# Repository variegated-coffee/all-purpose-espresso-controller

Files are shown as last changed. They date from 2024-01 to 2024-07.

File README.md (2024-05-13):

# All Purpose Espresso Controller

Espresso electronics are usually proprietary affairs with little to no expandability. The purpose of this project is to give everyone an open source alternative with lots of features and flexibility. 

It is designed to be useful in many different espresso machines, and for many different hardware configurations. It has the same PCB size as many very common Gicar controllers, making it fairly easy to swap this board into your existing enclosure. It also comes with screw holes, so a 3D printed enclosure is another option.

There's also a [corresponding 100-240 VAC board](https://github.com/open-lcc/all-purpose-espresso-controller-hv-board), with relays and an AC/DC converter, designed to also fit into those same Gicar enclosures.

## High-level features

* RP2040 microcontroller with 2 MB of program flash, and 2 MB of settings flash
* ESP32-S3 for extra processing power and Wi-fi/Bluetooth connectivity
* SD card reader
* Plenty of IO, at 12V, 5V and 3V3 levels
* Dedicated connector for a UART based user interface device, like an [Open LCC](https://github.com/open-lcc/open-lcc-board) or a Nextion touchscreen (selectable 5V or 3V3 level)
* EyeSPI connector for ESP32-S3
* ADS124S08 ADC (intended for e.g. pressure transducers or NTCs)
* FDC1004 Capacitance-to-digital (inteded for e.g. water level probes or capitance based controls)
* QWIIC ports (one per microcontroller) for additional expandability

[IBOM](https://raw.githack.com/open-lcc/all-purpose-espresso-controller/r0d/manufacturing-data/r0d/ibom.html)

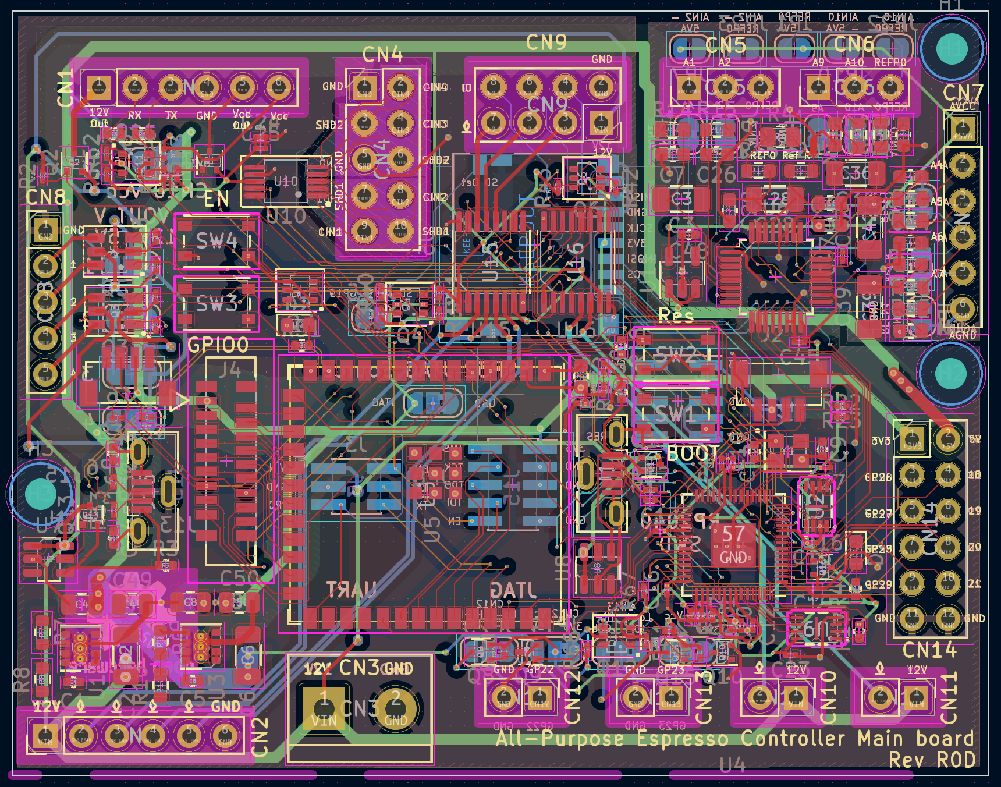
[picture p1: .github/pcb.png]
PCB

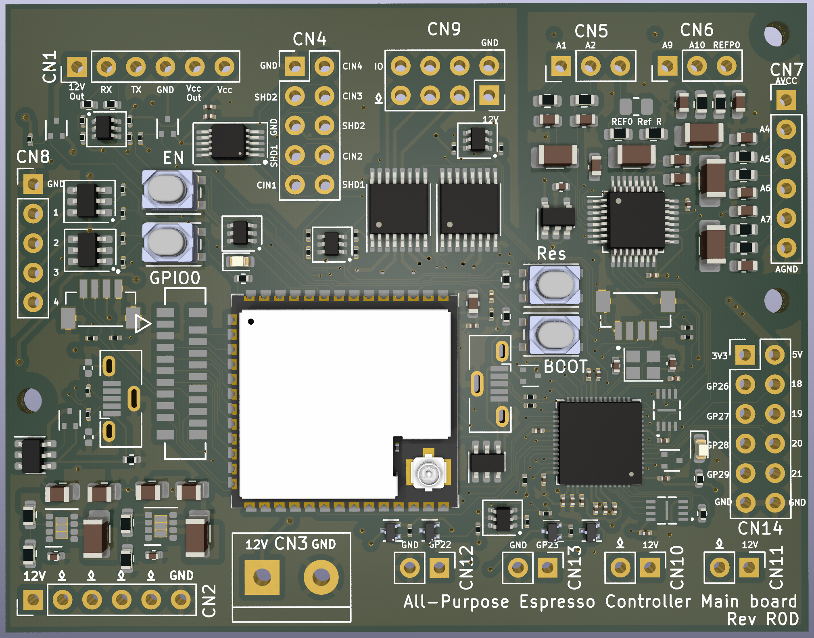
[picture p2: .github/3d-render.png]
3D render PCB 3D render

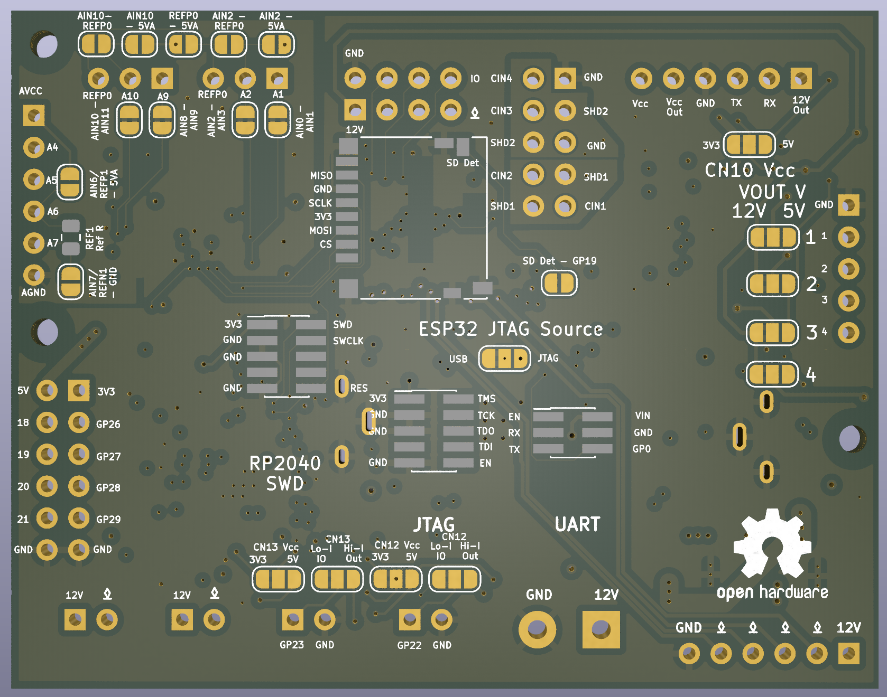
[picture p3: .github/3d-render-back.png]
3D render back PCB 3D render of back side


## Project status

The current hardware revision is R0D. It hasn't been manufactured yet, and you shouldn't be the first one to do it.

## Disclaimer

Anything you do with this, you do at your own risk. This hardware hasn't even been manufactured by it's creator yet. Your machine uses both line voltage power, high pressured hot water, steam and other dangerous components. You *really* shouldn't be using this yet; in fact, you shouldn't even consider it. Risks include but are not limited to, damaging your machine, personal injury, property damage and summoning dead Cthulhu from his sleep at R'lyeh.

## Connectivity
* CN1 - Display Connector, either for Open LCC or a Nextion Display
  * UART (selectable 3V3 or 5V, default 3V3)
    * JP9 selects voltage
    * RP2040 UART0
    * ESP32 GPIO17/GPIO14
  * 1x 12V output (SR2 DRAIN6)
  * 1x 3V3 output (SR2 DRAIN7)
  * 1 3V3/5V pin and GND pin
* CN2 - HV Board Connector
  * 12V and GND
  * 4 Open drains (SR1 DRAIN0-3)
* CN3 - Separate PSU Connector
  * 12V and GND
* CN4 - Capacitive sense connector
* CN5 - ADC port
  * See note below
* CN6 - ADC port
  * See note below
* CN7 - ADC port
  * See note below
* CN8 - Outputs
  * 4x 5V/12V Outputs
    * Voltage selectable by JP4-6/JP16
  * GND
* CN9 - Open drains and 3V3 IO
  * 3x Open drains (SR1 DRAIN5-7)
  * 3x 3V3 IO (RP2040 GPIO12-14)
  * 12V/GND
* CN10 - Open drain
  * SR2 DRAIN1
  * 12V
* CN11 - Open drain
  * SR2 DRAIN0
  * 12V
* CN12 - 3V3/5V GPIO
  * RP2040 GPIO22
  * Shifted through MOSFET level shifter
  * Can be switched to a 500 mA output with solder jumper
  * GND
* CN13 - 3V3/5V GPIO
  * RP2040 GPIO23
  * Shifted through MOSFET level shifter
  * Can be switched to a 500 mA output with solder jumper
  * GND
* CN14 - GPIO
  * RP2040 GPIO18-21
    * GP19 can be connected to SD Card Detect via a solder jumper
    * GP21 is also connected to an LED
  * RP2040 GPIO26-29
    * ADC Capable

### ADC
By default, CN5 and CN6 are configured for a ratiometric measurement. In order to use it as such, you need to fit a reference resistor for REF0. The reference resistor needs to be larger than the measured values (e.g. for a PT100, use a 400 ohm resistor), and needs to be high accuracy and low drift. 

AIN1-2, AIN4-7, and AIN9-10 are all outfitted with RC filters, as is REF0. The board is also designed in such a way that you can, by sacrificing an RC filter, convert a channel to instead use an upstream resistor divider. 

The ADS124S08 features two external references (REF0 and REF1), as well as an internal 2.5V reference. AIN6-7 double as REFP1/REFN1. The board is designed with footprints for a reference resistor.

#### Common configurations

##### PT100 RTD

##### PT1000 RTD

##### 50k NTC - Ratiometric

##### 50k NTC - Resistor divider

##### 0.3 – 4.5 V Pressure trandducer - 5 V Reference

##### 0.3 – 4.5 V Pressure trandducer - Resistor divider

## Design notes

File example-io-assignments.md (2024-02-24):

## Lelit Bianca v2 with Open LCC, Gear Pump, and Pump Pressure Transducer

### IO Assignment

* CN10 - Open LCC
* CN1 - Water level probe
* CN2 - Water tank level switch
* CN3 - Service Boiler NTC
* CN4 - Brew Boiler NTC
* CN5 - Brew Boiler SSR
* CN9 - Service Boiler SSR
* CN7 - Brew Switch
* JP2 Pin 3 - Water line / Low flow solenoid
* JP2 Pin 4 - Service boiler solenoid
* CN6 Pin 3 - Gear pump speed PWM
* CN6 Pin 5 - Gear Pump Tacheometer Input
* J11 Pin 2 - Pressure Transducer Analog Input

### Configuration

* ADC Vcc - 5V
* CN10 Vcc - 3V3
* DNF ESP32

## Rancilio Silvia with ESP32, SSD1309 display, Rotary encoder, Gear Pump, and Pump Pressure Transducer

### IO Assignment

* CN10 - Open LCC
* CN4 - Boiler NTC
* CN5 - Boiler SSR
* J12 Pin 8 - Display MOSI
* J12 Pin 4 - Display SCLK
* J12 Pin 6 - Display RES
* J12 Pin 10 - Display DC
* Hard-wire Display CS
* CN7 - Brew Switch
* CN2 - Water Switch
* J12 Pin 9 - Steam Switch
* J12 Pin 3 - Rotary Encoder Clk
* J12 Pin 5 - Rotary Encoder D
* J12 Pin 7 - Rotary Encoder SW
* JP2 Pin 4 - Three-way solenoid
* CN6 Pin 3 - Gear pump speed PWM
* CN6 Pin 5 - Gear Pump Tacheometer Input
* J11 Pin 2 - Pressure Transducer Analog Input

### Configuration

* ADC Vcc - 5V
* CN10 Vcc - 3V3
* DNF ESP32

## Worst case scenario IO Assignment

### Machine spec

* 2 group triple boiler (2 coffee, 1 service), all PID controlled with level sensors
* Dual PWM gear pumps for coffee boilers
* Single rotary pumps for service boiler
* Dual flow sensors
* Triple NTC thermistors
* Triple pressure transducers
* Five solenoids (3 line solenoids, 2 three-way group solenoid)
* Two brew microswitches
* One water tank level switch

### IO Assignments

* Brew Boiler 1 HE Relay - JP2 Pin 2
* Brew Boiler 2 HE Relay - JP2 Pin 3
* Service Boiler HE Relay - JP2 Pin 4
* Service Boiler Rotary Pump Relay - JP2 Pin 5
* Gear pump 1 PWM - CN6 Pin 3
* Gear pump 2 PWM - CN6 Pin 5
* Flow sensor 1 - J12 Pin 4 GP18
* Flow sensor 2 - J12 Pin 6 GP19
* NTC Brew 1 - CN3
* NTC Brew 2 - CN4
* NTC Service - J11 Pin 2
* Pressure Transducer 1 - J12 Pin 3 GP26
* Pressure Transducer 2 - J12 Pin 5 GP27
* Pressure Transducer 3 - J12 Pin 7 GP28
* Brew Boiler 1 Level sensor - J14 Pin 2
* Brew Boiler 2 Level sensor - J14 Pin 4
* Service Boiler Level sensor - CN1
* Water Tank Switch - CN6 Pin 7
* Brew switch 1 - CN2
* Brew switch 2 - CN7
* Solenoid 1 - J10 Pin 2
* Solenoid 2 - J10 Pin 3
* Solenoid 3 - CN6 Pin 4
* Solenoid 4 - CN6 Pin 6
* Solenoid 5 - CN6 Pin 8
* ESP32 UART J12 Pin 8 GP20
* ESP32 UART J12 Pin 10 GP21
* ESP32 Firmware update J12 Pin 9 GP29

#### Free pins

* CN5 (Output)
* CN9 (Output)
* J10 Pin 4 (Output)
* J11 Pin 3 (ADC)
* J14 Pin 7 (Capacitance)

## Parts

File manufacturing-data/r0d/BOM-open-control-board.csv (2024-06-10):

Comment | Designator | Footprint | LCSC
0R | R32,R33 | R_0201_0603Metric | C106228
18K7 | R13,R3 | R_0402_1005Metric | C11476
1K | R5,R6 | R_0402_1005Metric | C11702
Q_PMOS-E_DUAL_Generic_SEP_S1G1D2S2G2D1 | Q3,Q5 | TSOT-23-6 | C124461
10 μF, 25 V, X7R | C2,C6 | C_1206_3216Metric | C13585
DMP21D0UT-7 | Q1,Q15,Q2,Q8 | SOT-523 | C150733
6.8 nF, 50V | C1,C48,C5 | C_0402_1005Metric | C1542
12 pF | C10,C9 | C_0402_1005Metric | C1547
330 nF | C46 | C_0603_1608Metric | C159798
BM04B-SRSS-TB(LF)(SN) | J17,J2 | JST_BM04B-SRSS-TB(LF)(SN) | C160390
RP2040 | U4 | QFN-56-1EP_7x7mm_P0.4mm_EP3.2x3.2mm | C2040
DMG1012T-7 | Q10,Q13,Q14,Q16,Q9 | SOT-523 | C20512
DMN63D8LDW | Q11,Q12,Q4,Q6,Q7 | SOT-363_SC-70-6 | C211422
STPIC6C595TTR | U15,U16 | TSSOP-16_4.4x5mm_P0.65mm | C222081
KT-0603W | D1,D2 | LED_0603_1608Metric | C2290
75K | R9 | R_0603_1608Metric | C23242
24K | R10 | R_0603_1608Metric | C23352
10K | R1,R19,R2,R22,R23,R28,R29,R30,R34,R36,R37,R38,R39,R40,R41,R42,R43,R59,R61,R62,R63,R64,R65,R67,R68,R69,R70 | R_0201_0603Metric | C242159
120R | R31,R44 | R_0402_1005Metric | C25079
4K7 | R17,R18 | R_0402_1005Metric | C25900
SW_Push | SW1,SW2,SW3,SW4 | SW4_PTS815 SJM 250 SMTR LFS_CNK | C2689510
27R | R11,R12 | R_0201_0603Metric | C273268
47R | R45,R46,R47,R48,R49 | R_0201_0603Metric | C273279
71K5 | R7 | R_0603_1608Metric | C278547
W25Q16JVUXIQ | U2,U9 | W25Q16JVUXIQ_WIN | C2843335
FDC1004 | U10 | VSSOP-10_3x3mm_P0.5mm | C2865994
ADS124S08IPBSR | U6 | LQFP-32_5x5mm_P0.5mm | C2870171
ESP32-S3-WROOM-1 | U5 | ESP32-S3-WROOM-1U | C3013946
Molex_0525591853 | J4 | CON_525591853_MOL | C3169221
5.1 nF, C0G | C26,C29,C35,C37,C38,C40,C41,C43,C44,C7 | C_0603_1608Metric | C3884201
100 nF, >10V, X6S | C12,C13,C14,C15,C16,C17,C18,C19,C20,C21,C23,C24,C27,C31,C45,C53,C54 | C_0201_0603Metric | C412246
1 uF, >6.3V, X5R | C11,C22,C25,C30,C47,C51 | C_0201_0603Metric | C426073
22 uF, 10V, X7T | C4,C49,C50,C8 | C_0805_2012Metric | C45783
LM5050-1 | U7,U8 | TSOT-23-6 | C473393
TPS82130 | U1,U3 | Texas_SIL0008D_MicroSiP-8-1EP_2.8x3mm_P0.65mm_EP1.1x1.9mm_ThermalVias | C473914
6K04 1% | R14,R15,R21,R24,R25,R26,R27,R35 | R_0603_1608Metric | C513554
XYDBPCNANF-12MHZ | Y1 | Crystal_SMD_2520-4Pin_2.5x2.0mm | C521567
USB_B_Micro | J1,J16 | USB_Micro-B_Molex-105133-0001 | C586226
22 uF, 6.3V, X5R | C32 | C_0603_1608Metric | C59461
TC2014-5.0VxCTTR | U11 | SOT-23-5 | C626522
4K99 1% | R16,R20 | R_0603_1608Metric | C705903
51 nF, C0G | C28,C3,C36 | C_1206_3216Metric | C711044
13K3 | R8 | R_0603_1608Metric | C719290

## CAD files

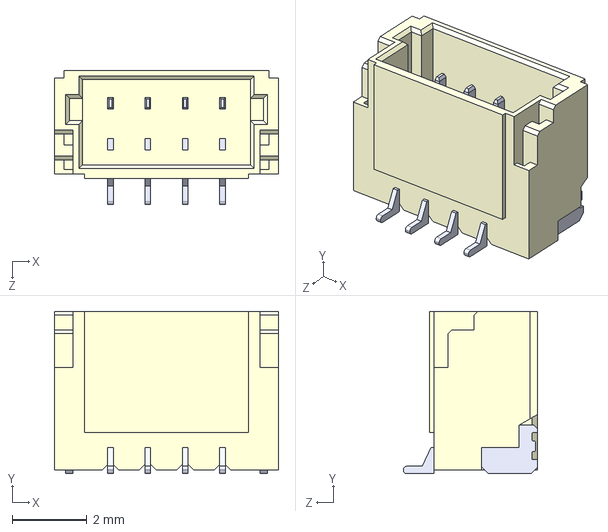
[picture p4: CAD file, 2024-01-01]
BM04B-SRSS-TB_LF__SN_/BM04B-SRSS-TB_LF__SN_.step
6.00 x 4.35 x 3.60 mm

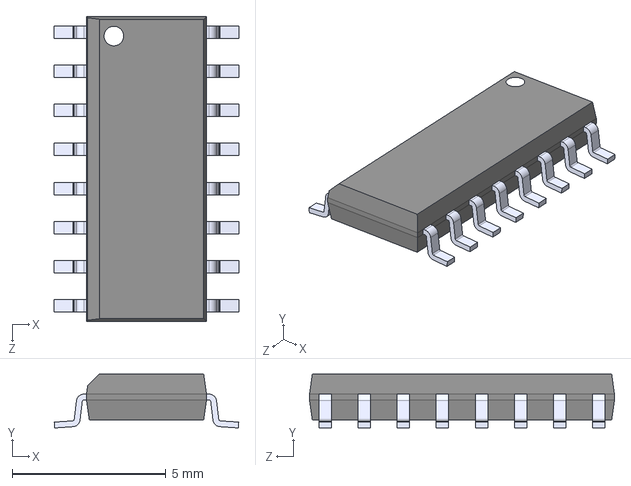
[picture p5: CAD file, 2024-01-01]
TPIC6C595DG4/TPIC6C595DG4.step
5.99 x 1.75 x 9.91 mm

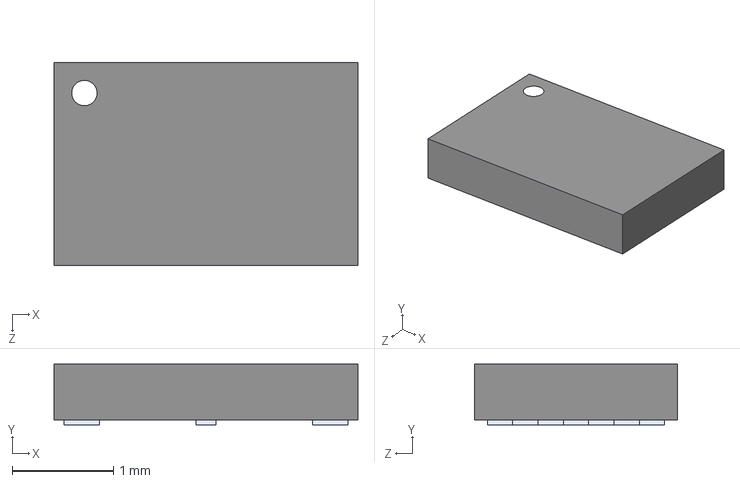
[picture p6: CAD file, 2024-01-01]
W25Q16JVUXIQ/W25Q16JVUXIQ.step
3.00 x 0.6 x 2.00 mm

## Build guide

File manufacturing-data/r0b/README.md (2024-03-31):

# Manufacturing with JLCPCB

Manufacturing of R0B was done with JLCPCB, including PCB Assembly.

The following settings were used:

### PCB Prototype
* Gerber file: GERBER-open-control-board_Y54
* Build Time: 3 days (PCBA Only)
* Base Material: FR-4 
* Layers: 4
* Dimension: 69 mm* 54 mm 
* PCB Qty: 5
* Product Type: Industrial/Consumer electronics 
* Different Design: 1
* Delivery Format: Single PCB 
* PCB Thickness: 1.6
* Impedance Control: no No requirement 
* Layer Sequence: 
* PCB Color: Green 
* Silkscreen: White
* Material Type: FR4-Standard TG 135-140 
* Via Covering: Epoxy Filled & Capped
* Surface Finish: HASL(with lead) 
* Deburring/Edge rounding: No
* Outer Copper Weight: 1 oz 
* Inner Copper Weight: 0.5 oz
* Gold Fingers: No 
* Flying Probe Test: Fully Test
* Castellated Holes: no 
* Edge Plating: No
* Remove Order Number: No 
* Min via hole size/diameter: 0.3mm/(0.4/0.45mm)
* 4-Wire Kelvin Test: No 
* Paper between PCBs: No
* Appearance Quality: IPC Class 2 Standard 
* Confirm Production file: Yes
* Silkscreen Technology: Ink-jet/Screen Printing Silkscreen 
* Package Box: With JLCPCB logo
* Board Outline Tolerance: ±0.2mm(Regular)

The observant will note that this is the default settings, except Via Covering and Confirm Production File.

### PCBA

* PCBA Type: Economic
* Assembly Side: Top Side
* PCBA Qty: 5
* Tooling holes: Added by JLCPCB
* Confirm Parts Placement: Yes
* Photo Confirmation: No
* Board Cleaning: No
* Conformal Coating: No
* Bake Components: No
* Packaging: Antistatic bubble film
* Depanel boards & edge rail before delivery: No
* Solder Paste: Sn96.5%, Ag3.0%, Cu0.5%(260℃)
* Others: No
* Add paste for unpopulated pad & step stencil opening: No
* File provided as: Complete File, just proceed with my own files
* Panel Format: 1 * 1
* Build Time: 1-2 days

Except for "Confirm Production File", this too is the default settings.

Economic PCBA doesn't allow for assembling the ESP32-S3, but it is fairly easy to solder on yourself, which is what I'll be doing.

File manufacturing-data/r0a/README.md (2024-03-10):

# Manufacturing data R0A - Do not manufacture

This revision is simply not working. There are several design flaws in it, which make it unusable for anything but validation, and even that requires desoldering chips, cutting traces, and bodging them. Do not manufacture it.

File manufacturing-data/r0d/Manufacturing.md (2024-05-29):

# All-purpose Espresso Controller R0D Manufacturing

## PCB Manufacturing parameters (JLCPCB)

* 6 layer board
* Material: FR-4 TG155
* Surface finish: ENIG
* Outer copper weight: 1oz
* Inner copper weight: 1oz
* Via covering: Epoxy filled and capped
* Min via hole size: 0.2 mm

## PCBA parameters (JLCPCB)

* PCBA Type: Standard
* Assembly side: Top side (You *could* do both sides, but the SD Card reader is reasonable easy to hand solder)

## PCB and PCBA price:
Approximately $520 ex VAT for a 10 board run.

## Additional components

In addition to the components in the JLCPCB BOM, you'll need some other (hand soldered) components.

* Connectors CN1, CN7
	* Cheapest option is Dupont style pin headers
	* Recommended: TE AMPMODU Mod 2, either angled or straight (depending on mounting preference)
* Connector CN2
	* Depends entirely on mounting
	* Recommended: 2.5 mm pitch ribbon cable, 6 positions, 0.75 mm^2 conductor, 3 cm length
* Connector CN3
	* Optional
	* Recommended: 2 pin screw terminal
* Connector CN4
	* Cheapest option is Dupont style pin headers
	* Other options include
		* TE AMPMODU Mod 2, 2 pin angled (single channel)
		* TE AMPMODU Mod 2, 5x2 pin straight
* Connectors CN10, CN11, CN12, CN13
	* Cheapest option is Dupont style pin headers
	* Recommended: TE AMPMODU Mod 2, either angled or straight (depending on mounting preference)
* Connectors CN5, CN6
	* Cheapest option is Dupont style pin headers
	* Other options include:
		* TE AMPMODU Mod 2, 2 pin either angled or straight
		* TE AMPMODU Mod 2, 3 pin either angled or straight
* Connector CN7
	* Cheapest option is Dupont style pin headers
* Connector CN14
	* Cheapest option is Dupont style pin headers
* REF0 Reference resistor
	* Recommended values
		* PT100: 470 ohm
		* PT1000: 4.7 kohm
		* 50K NTC: 470 kohm
* SD card reader
	* Hirose DM3D-SF
* RP2040 SWD Debug Connector J13
	* ARM Cortex Debug Connector 10-pin, 0.05"
	* Recommended: DNF
	* Example: Samtec FTSH-105-01-L-DV-007-K  
* ESP32-S3 JTAG Connector J15
	* ESP-Prog JTAG connector, 10-pin, 0.05"
	* Recommended: DNF
	* Example: Samtec FTSH-105-01-L-DV-007-K
* ESP32-S3 PROG Connector J3
	* ESP-Prog PROG connector, 6 pin, 0.05"
	* Recommended: DNF
	* Example: https://www.aliexpress.com/item/32951697063.html

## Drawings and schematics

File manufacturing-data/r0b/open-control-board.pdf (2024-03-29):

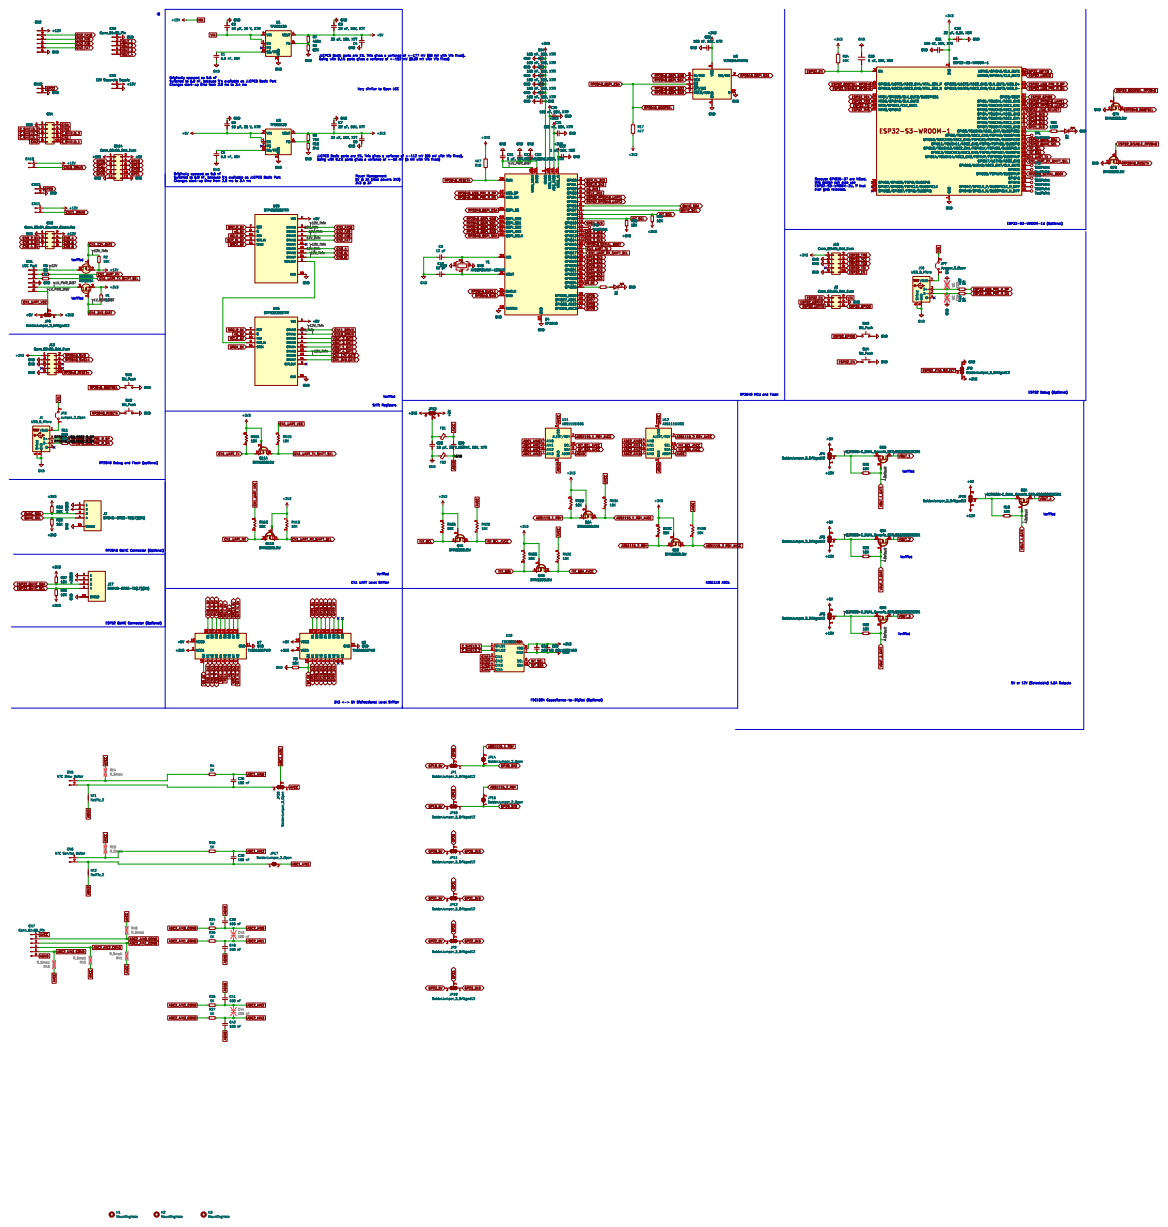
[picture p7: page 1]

3 VOUT 4 FB 6 PG 7 SS/TR 8 U1 TPS82130 GND

3 VOUT 4 FB 6 PG 7 SS/TR 8 C3

3 GND NC C34 U5ESP32-S3-WROOM-1 GND
RP2040_SERIAL_BOOT ESP32_U0RXD

3 VOUT 4 FB 6 PG 7 SS/TR 8 GND

3 VOUT 4 FB 6 PG 7 SS/TR 8 U3 TPS82130 GND

1 GPIO8 11 GPIO9 12 GPIO10 13 GPIO11 14 GPIO12 15 GPIO13 16 GPIO14 17 GPIO15 18 TESTEN 19 GPIO0 2 XIN 20 XOUT 21 DVDD 23 SWCLK 24 SWD 25 RUN 26 GPIO16 27 GPIO17 28 GPIO18 29 GPIO1 3 GPIO19 30 GPIO20 31 GPIO21 32 GPIO22 34 GPIO23 35 GPIO24 36 GPIO25 37 GPIO26_ADC0 38 GPIO27_ADC1 39 GPIO2 4 GPIO28_ADC2 40 GPIO29_ADC3 41 ADC_AVDD 43 VREG_IN 44 VREG_VOUT 45 USB_DM 46 USB_DP 47 USB_VDD 48 GPIO3 5 QSPI_SD3 51 QSPI_SCLK 52 QSPI_SD0 53 QSPI_SD2 54 QSPI_SD1 55 QSPI_SS 56 GND 57 GPIO4 6 GPIO5 7 GPIO6 8 GPIO7 9 GND GND D1 TP8 TestPoint +3V3

1 GPIO8 11 GPIO9 12 GPIO10 13 GPIO11 14 GPIO12 15 GPIO13 16 GPIO14 17 GPIO15 18 TESTEN 19 GPIO0 2 XIN 20 XOUT 21 DVDD 23 SWCLK 24 SWD 25 RUN 26 GPIO16 27 GPIO17 28 GPIO18 29 GPIO1 3 GPIO19 30 GPIO20 31 GPIO21 32 GPIO22 34 GPIO23 35 GPIO24 36 GPIO25 37 GPIO26_ADC0 38 GPIO27_ADC1 39 GPIO2 4 GPIO28_ADC2 40 GPIO29_ADC3 41 ADC_AVDD 43 VREG_IN 44 VREG_VOUT 45 USB_DM 46 USB_DP 47 USB_VDD 48 GPIO3 5 QSPI_SD3 51 QSPI_SCLK 52 QSPI_SD0 53 QSPI_SD2 54 QSPI_SD1 55 QSPI_SS 56 GND 57 GPIO4 6 GPIO5 7 GPIO6 8 GPIO7 9 U4 RP2040

3 AIN0 4 AIN1 5 AIN2 6 AIN3 7 VDD
ADDR 1 SCL 10 ALERT/RDY 2 GND

CN1 UART Level Shifter Verified

1 OE 10 GND 11 B8 12 B7 13 B6 14 B5 15 B4 16 B3 17 B2 18 VCCB 19 VCCA 2 B1 20 A2

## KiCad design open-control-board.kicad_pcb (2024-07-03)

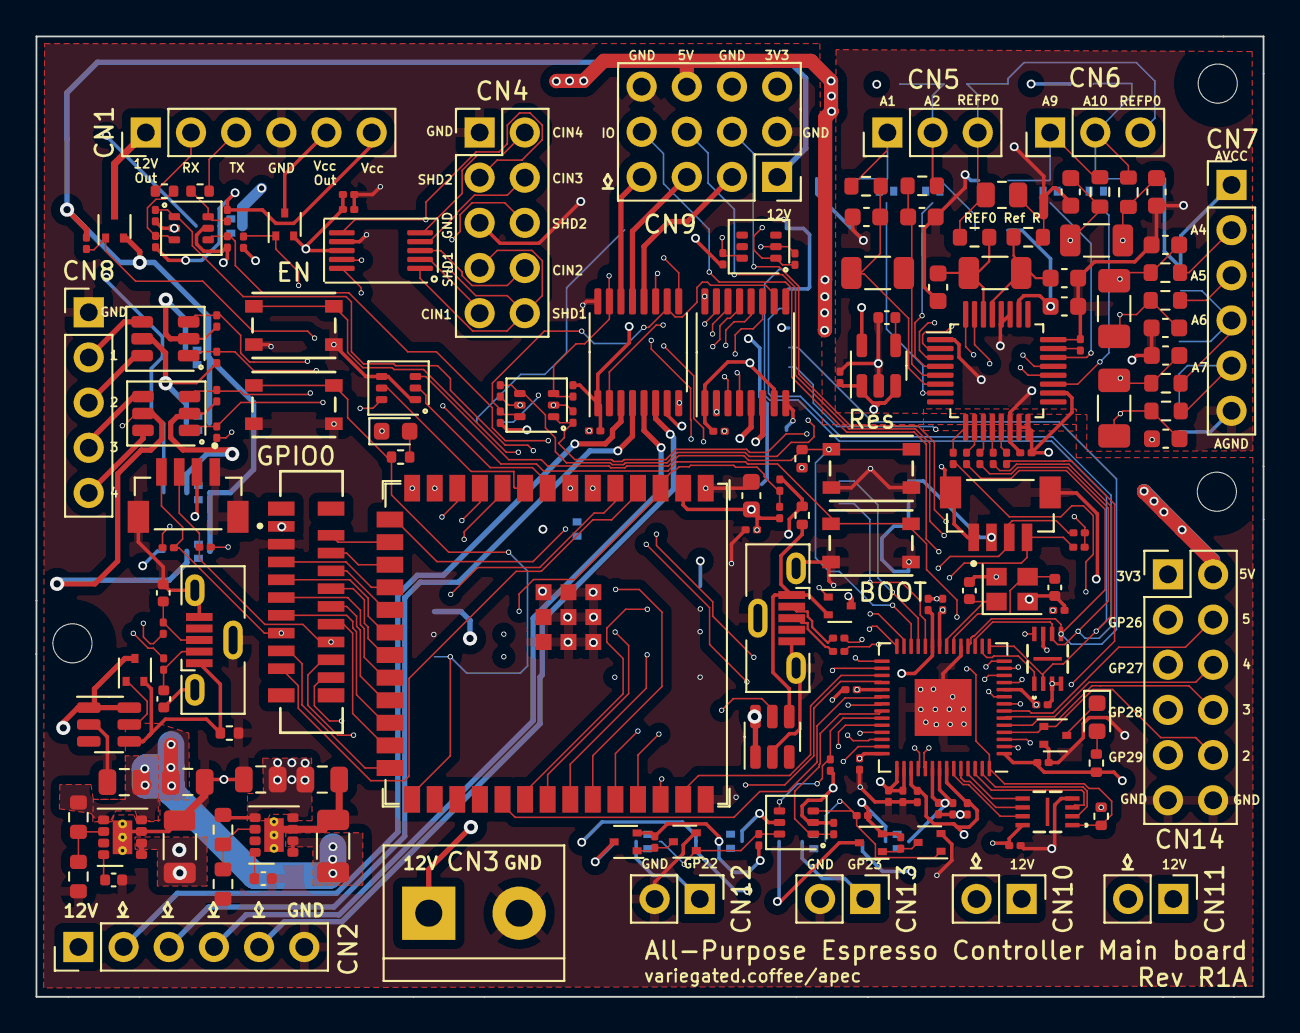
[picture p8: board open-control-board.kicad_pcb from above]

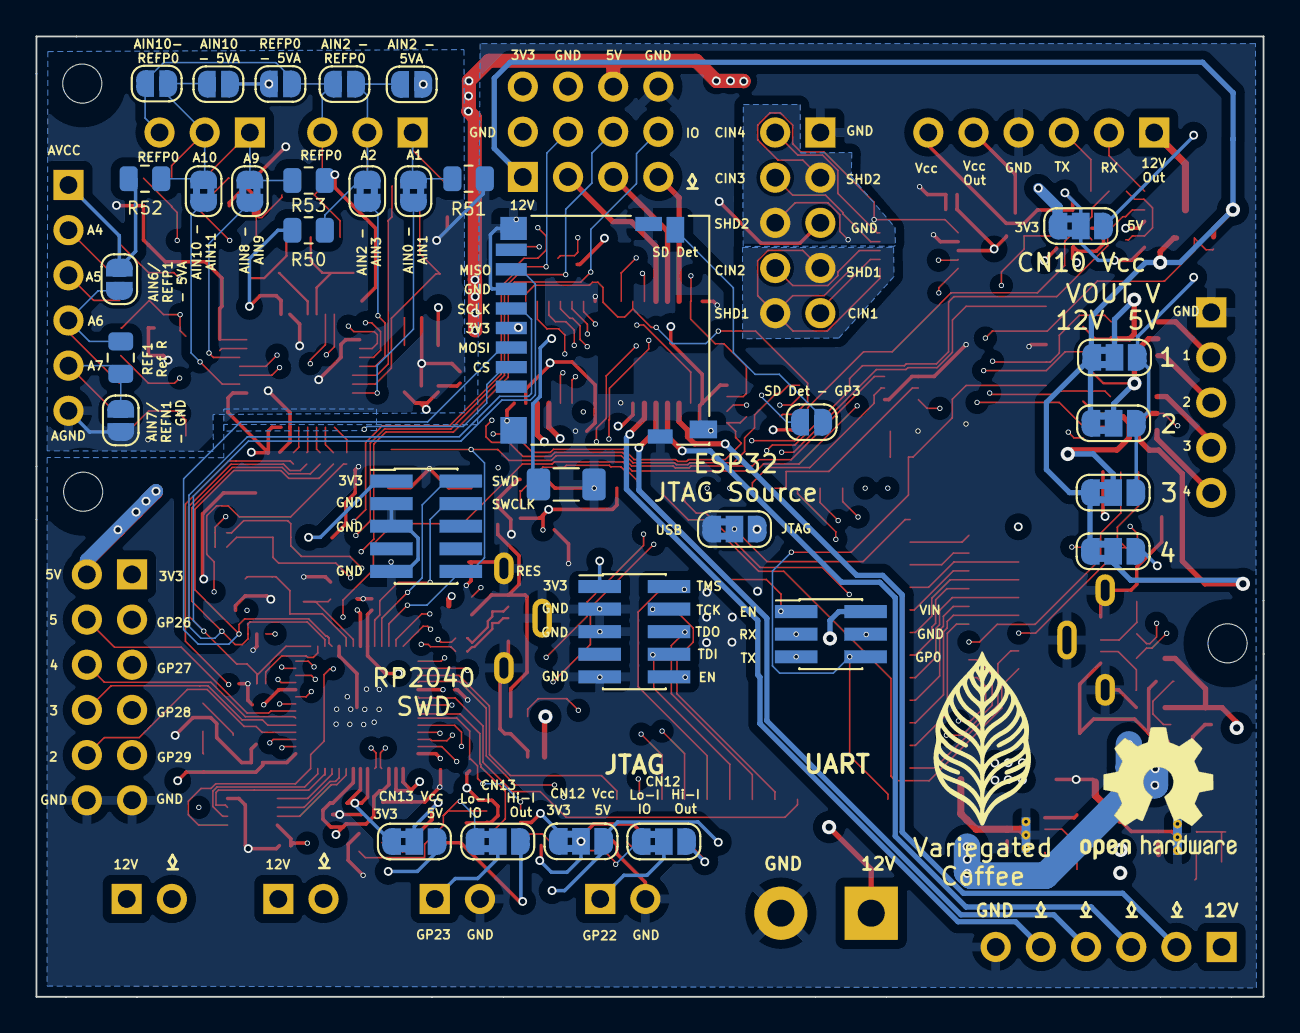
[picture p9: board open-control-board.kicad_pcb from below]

Board: 6 copper layers, 69.0 x 54.0 mm, 203 parts (32 on the bottom side), 175 nets.

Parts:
C1, C5, C48: 6.8 nF, 50V; C_0402_1005Metric
C2, C6: 10 μF, 25 V, X7R; C_1206_3216Metric
C3, C28, C36: 51 nF, C0G; C_1206_3216Metric
C4, C8, C49, C50: 22 uF, 10V, X7T; C_0805_2012Metric
C7, C26, C29, C35, C37, C38, C40, C41, C43, C44: 5.1 nF, C0G; C_0603_1608Metric
C9, C10: 12 pF; C_0402_1005Metric
C11, C22, C25, C30, C47, C51: 1 uF, >6.3V, X5R; C_0201_0603Metric
C12, C13, C14, C15, C16, C17, C18, C19, C20, C21, C23, C24, C27, C31, C45, C53, C54: 100 nF, >10V, X6S; C_0201_0603Metric
C32: 22 uF, 6.3V, X5R; C_0603_1608Metric
C33, C34: NC; C_0402_1005Metric
C39, C42: C_Small; C_1206_3216Metric_Pad1.33x1.80mm_HandSolder
C46: 330 nF; C_0603_1608Metric
C52: 47 uF; C_1206_3216Metric_Pad1.33x1.80mm_HandSolder
CN1: LCC Port; PinHeader_1x06_P2.54mm_Vertical
CN2, CN7: Conn_01x06_Pin; PinHeader_1x06_P2.54mm_Vertical
CN3: 12V Separate Supply; TerminalBlock_bornier-2_P5.08mm
CN4: Conn_02x05_Counter_Clockwise; PinHeader_2x05_P2.54mm_Vertical
CN5: NTC Brew Boiler; PinHeader_1x03_P2.54mm_Vertical
CN6: NTC Service Boiler; PinHeader_1x03_P2.54mm_Vertical
CN8: Conn_01x05_Pin; PinHeader_1x05_P2.54mm_Vertical
CN9: Conn_3x04
CN10, CN11, CN12, CN13: PinHeader_1x02_P2.54mm_Vertical
CN14: Conn_02x06_Odd_Even; PinHeader_2x06_P2.54mm_Vertical
D1, D2: KT-0603W; LED_0603_1608Metric
H1, H2, H3: MountingHole; MountingHole_2.2mm_M2
J1, J16: USB_B_Micro; USB_Micro-B_Molex-105133-0001
J2, J17: BM04B-SRSS-TB(LF)(SN); JST_BM04B-SRSS-TB(LF)(SN)
J3: Conn_02x03_Odd_Even; PinHeader_2x03_P1.27mm_Vertical_SMD
J4: Molex_0525591853; CON_525591853_MOL
J5: Micro_SD_Card_Det_Hirose_DM3AT; microSD_HC_Hirose_DM3D-SF
J13, J15: Conn_02x05_Odd_Even; PinHeader_2x05_P1.27mm_Vertical_SMD
JP1, JP2, JP3, JP7, JP10, JP15, JP22, JP23: SolderJumper_2_Open; SolderJumper-2_P1.3mm_Open_RoundedPad1.0x1.5mm
JP4, JP5, JP6, JP8, JP9, JP16, JP18, JP19, JP24, JP25: SolderJumper_3_Bridged12; SolderJumper-3_P1.3mm_Bridged2Bar12_RoundedPad1.0x1.5mm_Num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
JP13, JP17, JP20, JP21: SolderJumper_2_Bridged; SolderJumper-2_P1.3mm_Bridged2Bar_RoundedPad1.0x1.5mm
NT1: NetTie_2; NetTie-2_SMD_Pad0.5mm
Q1, Q2, Q8, Q15: DMP21D0UT-7; SOT-523
Q3, Q5: Q_PMOS-E_DUAL_Generic_SEP_S1G1D2S2G2D1; TSOT-23-6
Q4, Q6, Q7, Q11, Q12: DMN63D8LDW; SOT-363_SC-70-6
Q9, Q10, Q13, Q14, Q16: DMG1012T-7; SOT-523
R1, R2, R19, R22, R23, R28, R29, R30, R34, R36, R37, R38, R39, R40, R41, R42, R43, R59, R61, R62, R63, R64, R65, R67, R68, R69, R70: 10K; R_0201_0603Metric
R3, R13: 18K7; R_0402_1005Metric
R4, R50, R51, R52, R53, R66: R_Small; R_0805_2012Metric
R5, R6: 1K; R_0402_1005Metric
R7: 71K5; R_0603_1608Metric
R8: 13K3; R_0603_1608Metric
R9: 75K; R_0603_1608Metric
R10: 24K; R_0603_1608Metric
R11, R12: 27R; R_0201_0603Metric
R14, R15, R21, R24, R25, R26, R27, R35: 6K04 1%; R_0603_1608Metric
R16, R20: 4K99 1%; R_0603_1608Metric
R17, R18: 4K7; R_0402_1005Metric
R31, R44: 120R; R_0402_1005Metric
R32, R33: 0R; R_0201_0603Metric
R45, R46, R47, R48, R49: 47R; R_0201_0603Metric
SW1, SW2, SW3, SW4: SW_Push; SW4_PTS815 SJM 250 SMTR LFS_CNK
U1, U3: TPS82130; Texas_SIL0008D_MicroSiP-8-1EP_2.8x3mm_P0.65mm_EP1.1x1.9mm_T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
U2, U9: W25Q16JVUXIQ; W25Q16JVUXIQ_WIN
U4: RP2040; QFN-56-1EP_7x7mm_P0.4mm_EP3.2x3.2mm
U5: ESP32-S3-WROOM-1; ESP32-S3-WROOM-1U
U6: ADS124S08IPBSR; LQFP-32_5x5mm_P0.5mm
U7, U8: LM5050-1; TSOT-23-6
U10: FDC1004; VSSOP-10_3x3mm_P0.5mm
U11: TC2014-5.0VxCTTR; SOT-23-5
U15, U16: STPIC6C595TTR; TSSOP-16_4.4x5mm_P0.65mm
Y1: XYDBPCNANF-12MHZ; Crystal_SMD_2520-4Pin_2.5x2.0mm

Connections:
+3V3: C8.1, C14.2, C15.2, C16.2, C17.2, C18.2, C19.2, C20.1, C21.1, C22.1, C23.2, C24.1, C25.1, C27.2, C31.2, C32.2, C45.1, C50.1, C52.1, CN9.9, CN14.1, J2.2, J4.1 (Vcc), J5.4 (VDD), J13.1, J15.1, J17.2, JP8.3 (B), JP9.1 (A), JP19.1 (A), JP24.1 (A), Q1.2 (S), Q4.2 (G1), Q4.5 (G2), Q6.2 (G1), Q11.2 (G1), Q11.5 (G2), Q12.2 (G1), Q12.5 (G2), R1.1, R9.1, R17.2, R18.2, R22.2, R23.1, R34.1, R36.2, R37.1, R38.1, R40.1, R42.1, R44.1, R61.1, R62.1, R65.1, R67.1, U2.8 (VCC), U3.4 (VOUT), U3.5 (VOUT), U4.1 (IOVDD), U4.10 (IOVDD), U4.22 (IOVDD), U4.33 (IOVDD), U4.42 (IOVDD), U4.43 (ADC_AVDD), U4.44 (VREG_IN), U4.48 (USB_VDD), U4.49 (IOVDD), U5.2 (3V3), U6.15 (IOVDD), U6.16 (DVDD), U6.18 (RESET_N), U9.8 (VCC), U10.8 (VDD)
+5V: C4.1, C6.2, C49.1, C51.1, C53.2, C54.2, CN9.11, CN14.2, JP4.3 (B), JP5.3 (B), JP6.3 (B), JP9.3 (B), JP16.3 (B), JP19.3 (B), JP24.3 (B), R7.1, R39.1, R41.1, R43.1, U1.4 (VOUT), U1.5 (VOUT), U3.1 (EN), U3.2 (VIN), U11.1 (VIN), U11.3 (ON/~OFF), U15.1 (VCC), U15.7 (~CLR), U16.1 (VCC), U16.7 (~CLR)
+5VA: C46.1, CN7.1, JP1.1 (A), JP2.1 (A), JP7.1 (A), JP10.1 (A), R50.2, R52.2, U6.26 (AVDD), U11.5 (VOUT)
/RP2040_USB_POST_R_DN: J1.2 (D-), R12.1
/RP2040_USB_POST_R_DP: J1.3 (D+), R11.1
ADC_CS: R49.2, U4.2 (GPIO0)
ADC_DRDY: R45.2, U4.35 (GPIO23)
AIN0: JP13.2 (B), U6.7 (AIN0)
AIN1: C3.2, C7.1, R14.2, U6.6 (AIN1)
AIN1_COND: CN5.1, JP13.1 (A), R14.1, R51.1
AIN2: C3.1, C26.2, R15.1, U6.5 (AIN2)
AIN2_COND: CN5.2, JP7.2 (B), JP17.2 (B), JP23.2 (B), R15.2, R50.1
AIN3: JP17.1 (A), U6.4 (AIN3)
AIN4: C42.2, C43.1, R27.2, U6.3 (AIN4)
AIN4_COND: CN7.2, R27.1
AIN5: C42.1, C44.2, R35.1, U6.2 (AIN5)
AIN5_COND: CN7.3, R35.2
AIN6_REFP1: C39.2, C40.1, R25.2, U6.32 (REFP1_AIN6)
AIN6_REFP1_COND: CN7.4, JP2.2 (B), R25.1, R66.1
AIN7_REFN1: C39.1, C41.2, R26.1, U6.31 (REFN1_AIN7)
AIN7_REFN1_COND: CN7.5, JP3.2 (B), R26.2, R66.2
AIN8: JP20.2 (B), U6.22 (GPIO0_AIN8)
AIN9: C36.2, C37.1, R21.2, U6.21 (GPIO1_AIN9)
AIN9_COND: CN6.1, JP20.1 (A), R21.1, R53.1
AIN10: C36.1, C38.2, R24.1, U6.20 (GPIO2_AIN10)
AIN10_COND: CN6.2, JP10.2 (B), JP21.2 (B), JP22.2 (B), R24.2, R52.1
AIN11: JP21.1 (A), U6.19 (GPIO3_AIN11)
CIN1: CN4.9, U10.2 (CIN1)
CIN2: CN4.8, U10.3 (CIN2)
CIN3: CN4.4, U10.4 (CIN3)
CIN4: CN4.2, U10.5 (CIN4)
CN1_3V3_GATE: Q1.1 (G), R1.2, U16.14 (DRAIN7)
CN1_12V_GATE: Q2.1 (G), R2.1, U16.13 (DRAIN6)
CN1_UART_RX: Q11.3 (D2), R5.2, R64.2
CN1_UART_RX_SHIFT_SEL: Q11.4 (S2), R65.2, U4.28 (GPIO17), U5.7 (GPIO7/TOUCH7/ADC1_CH6)
CN1_UART_TX: Q11.1 (S1), R62.2, U4.27 (GPIO16), U5.6 (GPIO6/TOUCH6/ADC1_CH5)
CN1_UART_TX_SHIFT_SEL: Q11.6 (D1), R6.2, R63.2
CN1_UART_VCC: CN1.6, JP9.2 (C), R63.1, R64.1
CN2_FA7: CN2.5, U15.6 (DRAIN3)
CN2_FA8: CN2.4, U15.5 (DRAIN2)
CN2_FA9: CN2.3, U15.4 (DRAIN1)
CN2_FA10: CN2.2, U15.3 (DRAIN0)
CN9_3: CN9.3, U15.12 (DRAIN5)
CN9_4: CN9.4, U4.12 (GPIO9)
CN9_5: CN9.5, U15.13 (DRAIN6)
CN9_6: CN9.6, U4.13 (GPIO10)
CN9_7: CN9.7, U15.14 (DRAIN7)
CN9_8: CN9.8, U4.14 (GPIO11)
CN10_DRAIN: CN10.2, U16.5 (DRAIN2)
CN11_DRAIN: CN11.2, U16.6 (DRAIN3)
CN12: CN12.1, JP25.2 (C)
CN12_3V3: Q12.1 (S1), R61.2, U4.36 (GPIO24)
CN12_HighI: JP25.3 (B), Q8.3 (D)
CN12_LowI: JP25.1 (A), Q9.1 (G), Q12.6 (D1), R68.2
CN12_VCC: JP19.2 (C), Q8.2 (S), R68.1, R70.2
CN13: CN13.1, JP18.2 (C)
CN13_3V3: Q12.4 (S2), R67.2, U4.37 (GPIO25)
CN13_HighI: JP18.3 (B), Q15.3 (D)
CN13_LowI: JP18.1 (A), Q10.1 (G), Q12.3 (D2), R69.2
CN13_VCC: JP24.2 (C), Q15.2 (S), R59.2, R69.1
CN14_3: CN14.3, U4.38 (GPIO26_ADC0)
CN14_4: CN14.4, U4.7 (GPIO5)
CN14_5: CN14.5, U4.39 (GPIO27_ADC1)
CN14_6: CN14.6, U4.6 (GPIO4)
CN14_7: CN14.7, U4.40 (GPIO28_ADC2)
CN14_8: CN14.8, JP15.1 (A), U4.5 (GPIO3)
CN14_9: CN14.9, U4.41 (GPIO29_ADC3)
CN14_10: CN14.10, Q16.1 (G), U4.4 (GPIO2)
C_SHIELD_1: CN4.7, CN4.10, U10.1 (SHLD1)
C_SHIELD_2: CN4.3, CN4.6, U10.6 (SHLD2)
ESP32_BOOTSEL_RP2040: Q7.2 (G1), U5.8 (GPIO15/U0RTS/ADC2_CH4/XTAL_32K_P)
ESP32_DISABLE_RP2040: Q7.5 (G2), U5.9 (GPIO16/U0CTS/ADC2_CH5/XTAL_32K_N)
ESP32_EN: C30.2, J3.1, J15.10, R34.2, SW4.1, U5.3 (EN)
ESP32_GPIO0: J3.6, R31.1, SW3.1, U5.27 (GPIO0/BOOT)
ESP32_JTAG_SELECT: JP8.2 (C), U5.15 (GPIO3/TOUCH3/ADC1_CH2)
ESP32_QWIIC_SCL: J4.13 (SCL), J17.4, R36.1, U5.12 (GPIO8/TOUCH8/ADC1_CH7/SUBSPICS1)
ESP32_QWIIC_SDA: J4.14 (SDA), J17.3, R37.2, U5.11 (GPIO18/U1RXD/ADC2_CH7/CLK_OUT3)
ESP32_RP2040_UART1: U4.31 (GPIO20), U5.39 (GPIO1/TOUCH1/ADC1_CH0)
ESP32_RP2040_UART2: U4.32 (GPIO21), U5.38 (GPIO2/TOUCH2/ADC1_CH1)
ESP32_TCK: J15.4, U5.32 (MTCK/GPIO39/CLK_OUT3/SUBSPICS1)
ESP32_TDI: J15.8, U5.34 (MTDI/GPIO41/CLK_OUT1)
ESP32_TDO: J15.6, U5.33 (MTDO/GPIO40/CLK_OUT2)
ESP32_TMS: J15.2, U5.35 (MTMS/GPIO42)
ESP32_U0RXD: J3.5, U5.36 (U0RXD/GPIO44/CLK_OUT2)
ESP32_U0TXD: J3.3, U5.37 (U0TXD/GPIO43/CLK_OUT1)
ESP32_USB_PRE_R_DN: R33.2, U5.13 (GPIO19/U1RTS/ADC2_CH8/CLK_OUT2/USB_D-)
ESP32_USB_PRE_R_DP: R32.2, U5.14 (GPIO20/U1CTS/ADC2_CH9/CLK_OUT1/USB_D+)
ESP32_USB_VBUS: J16.1 (VBUS), Q13.2 (S), R3.1, U7.4 (IN)
EYESPI_BL: J4.2 (BACKLIGHT), U5.16 (GPIO46)
EYESPI_BUSY_TE: J4.16 (BUSY/TE), U5.10 (GPIO17/U1TXD/ADC2_CH6)
EYESPI_DC: J4.7 (DC), U5.20 (GPIO12/TOUCH12/ADC2_CH1/FSPICLK/FSPIIO6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)
EYESPI_DISP_CS: J4.9 (DISP_CS), U5.22 (GPIO14/TOUCH14/ADC2_CH3/FSPIWP/FSPIDQS/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)
EYESPI_GPIO1: J4.17 (GPIO1), U5.4 (GPIO4/TOUCH4/ADC1_CH3)
EYESPI_GPIO2: J4.18 (GPIO2), U5.5 (GPIO5/TOUCH5/ADC1_CH4)
EYESPI_INT: J4.15 (INT), U5.26 (GPIO45)
EYESPI_MEM_CS: J4.11 (MEM_CS), U5.24 (GPIO47/SPICLK_P/SUBSPICLK_P_DIFF)
EYESPI_MISO: J4.6 (MISO), U5.19 (GPIO11/TOUCH11/ADC2_CH0/FSPID/FSPIIO5/S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)
EYESPI_MOSI: J4.5 (MOSI), U5.18 (GPIO10/TOUCH10/ADC1_CH9/FSPICS0/FSPIIO4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)
EYESPI_RESET: J4.8 (RESET), U5.21 (GPIO13/TOUCH13/ADC2_CH2/FSPIQ/FSPIIO7/S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)
EYESPI_SCK: J4.4 (SCK), U5.17 (GPIO9/TOUCH9/ADC1_CH8/FSPIHD/SUBSPIHD)
EYESPI_SD_CS: J4.10 (SD_CS), U5.23 (GPIO21)
EYESPI_TS_CS: J4.12 (TS_CS), U5.25 (GPIO48/SPICLK_N/SUBSPICLK_N_DIFF)
GND: C1.2, C2.1, C4.2, C5.2, C6.1, C7.2, C8.2, C9.2, C10.2, C11.2, C12.2, C13.2, C14.1, C15.1, C16.1, C17.1, C18.1, C19.1, C20.2, C21.2, C22.2, C23.1, C24.2, C25.2, C26.1, C27.1, C29.2, C30.1, C31.1, C32.1, C33.1, C34.2, C35.1, C37.2, C38.1, C40.2, C41.1, C43.2, C44.1, C45.2, C46.2, C47.2, C48.2, C49.2, C50.2, C51.2, C52.2, C53.1, C54.1, CN1.4, CN2.6, CN3.2, CN4.1, CN4.5, CN7.6, CN8.1, CN9.2, CN9.10, CN9.12, CN12.2, CN13.2, CN14.11, CN14.12, D2.1 (K), J1.5 (GND), J1.6 (Shield), J2.1, J2.S1 (SHIELD), J2.S2 (SHIELD), J3.4, J4.3 (GND), J5.6 (VSS), J5.10 (DET_A), J5.11 (SHIELD), J13.3, J13.5, J13.9, J15.3, J15.5, J15.9, J16.5 (GND), J16.6 (Shield), J17.1, J17.S1 (SHIELD), J17.S2 (SHIELD), JP3.1 (A), JP8.1 (A), NT1.1, Q7.1 (S1), Q7.4 (S2), Q9.2 (S), Q10.2 (S), Q16.2 (S), R3.2, R8.1, R10.1, R13.2, R51.2, R53.2, SW1.2, SW2.2, SW3.2, SW4.2, U1.3 (GND), U1.9 (GND), U2.3 (~WP/IO2), U2.4 (GND), U2.7 (~HOLD/IO3), U3.3 (GND), U3.9 (GND), U4.19 (TESTEN), U4.57 (GND), U5.1 (GND), U5.40 (GND), U5.41 (GND), U6.1 (AINCOM), U6.14 (DGND), U6.24 (REFCOM), U6.27 (AVSS), U6.28 (AVSS), U7.2 (GND), U8.2 (GND), U9.4 (GND), U10.7 (GND), U11.2 (GND), U15.8 (~G), U15.16 (GND), U16.8 (~G), U16.16 (GND), Y1.2, Y1.4
INT_SPI_MISO: J5.7 (DAT0), R46.2, U2.2 (SO/IO1), U4.15 (GPIO12)
INT_SPI_MOSI: J5.3 (CMD), R48.2, U2.5 (SI/IO0), U4.18 (GPIO15)
INT_SPI_SCLK: J5.5 (CLK), R47.2, U2.6 (SCK), U4.17 (GPIO14)
unnamed: CN1.1, Q2.3 (D)
unnamed: CN1.2, R5.1
unnamed: CN1.3, R6.1
unnamed: CN1.5, Q1.3 (D)
unnamed: D1.2 (A), R44.2
unnamed: D1.1 (K), Q16.3 (D)
unnamed: D2.2 (A), R31.2
unnamed: C33.2, J16.3 (D+), R32.1
unnamed: C34.1, J16.2 (D-), R33.1
unnamed: JP4.2 (C), Q5.2 (S2), R28.1
unnamed: JP5.2 (C), Q5.5 (S1), R29.1
unnamed: JP6.2 (C), Q3.2 (S2), R30.1
unnamed: JP16.2 (C), Q3.5 (S1), R19.1
unnamed: NT1.2, R4.2, R20.2
unnamed: Q8.1 (G), Q9.3 (D), R70.1
unnamed: Q10.3 (D), Q15.1 (G), R59.1
unnamed: Q13.1 (G), U7.5 (GATE)
unnamed: Q14.1 (G), U8.5 (GATE)
unnamed: R7.2, R8.2, U1.6 (FB)
unnamed: C1.1, U1.8 (SS/TR)
unnamed: R9.2, R10.2, U3.6 (FB)
unnamed: C5.1, U3.8 (SS/TR)
unnamed: C11.1, C12.1, C13.1, U4.23 (DVDD), U4.45 (VREG_VOUT), U4.50 (DVDD)
unnamed: C9.1, U4.20 (XIN), Y1.3
unnamed: C10.1, U4.21 (XOUT), Y1.1
unnamed: R49.1, U6.9 (CS_N)
unnamed: R48.1, U6.10 (DIN)
unnamed: R46.1, U6.12 (DOUT_DRDY_N)
unnamed: R45.1, U6.13 (DRDY_N)
unnamed: C47.1, U6.23 (REFOUT)
unnamed: R47.1, U6.11 (SCLK)
unnamed: C48.1, U11.4 (BP)
unnamed: U15.9 (SER_OUT), U16.2 (SER_IN)
QWIIC_SCL: J2.4, R22.1, U4.30 (GPIO19), U10.9 (SCL)
QWIIC_SDA: J2.3, R23.2, U4.29 (GPIO18), U10.10 (SDA), U15.11 (DRAIN4)
RCLK_3V3: Q4.1 (S1), R38.2, U4.9 (GPIO7)
RCLK_5V: Q4.6 (D1), R39.2, U15.10 (RCK), U16.10 (RCK)
REFN0: C28.1, C35.2, R20.1, U6.29 (REFN0)
REFP0: C28.2, C29.1, R16.2, U6.30 (REFP0)
REF_IN: CN5.3, CN6.3, JP1.2 (B), JP22.1 (A), JP23.1 (A), R4.1, R16.1
RP2040_BOOTSEL: Q7.6 (D1), R17.1, SW1.1, U4.56 (QSPI_SS), U9.1 (~CS)
RP2040_QSPI_SCK: U4.52 (QSPI_SCLK), U9.6 (SCK)
RP2040_QSPI_SD0: U4.53 (QSPI_SD0), U9.5 (SI/IO0)
RP2040_QSPI_SD1: U4.55 (QSPI_SD1), U9.2 (SO/IO1)
RP2040_QSPI_SD2: U4.54 (QSPI_SD2), U9.3 (~WP/IO2)
RP2040_QSPI_SD3: U4.51 (QSPI_SD3), U9.7 (~HOLD/IO3)
RP2040_RESETn: J13.10, Q7.3 (D2), R18.1, SW2.1, U4.26 (RUN)
RP2040_SERIAL_BOOT: U4.34 (GPIO22), U5.31 (GPIO38/FSPIWP/SUBSPIWP)
RP2040_SWCLK: J13.4, U4.24 (SWCLK)
RP2040_SWD: J13.2, U4.25 (SWD)
RP2040_USB_PRE_R_DN: R12.2, U4.46 (USB_DM)
RP2040_USB_PRE_R_DP: R11.2, U4.47 (USB_DP)
RP2040_USB_VBUS: J1.1 (VBUS), Q14.2 (S), R13.1, U8.4 (IN)
SD_CS: J5.2 (DAT3/CD), U4.3 (GPIO1)
SD_DET: J5.9 (DET_B), JP15.2 (B)
SER_IN_3V3: Q6.1 (S1), R42.2, U4.8 (GPIO6)
SER_IN_5V: Q6.6 (D1), R43.2, U15.2 (SER_IN)
SET_FLSH_CS: U2.1 (~CS), U4.16 (GPIO13)
SRCK_3V3: Q4.4 (S2), R40.2, U4.11 (GPIO8)
SRCK_5V: Q4.3 (D2), R41.2, U15.15 (SRCK), U16.15 (SRCK)
VIN: C2.2, CN2.1, CN3.1, CN9.1, CN10.1, CN11.1, J3.2, JP4.1 (A), JP5.1 (A), JP6.1 (A), JP16.1 (A), Q2.2 (S), Q13.3 (D), Q14.3 (D), R2.2, U1.1 (EN), U1.2 (VIN), U7.1 (VS), U7.6 (OUT), U8.1 (VS), U8.6 (OUT)
VOUT_1: CN8.2, Q5.4 (D2)
VOUT_1_GATE: Q5.3 (G2), R28.2, U16.12 (DRAIN5)
VOUT_2: CN8.3, Q5.6 (D1)
VOUT_2_GATE: Q5.1 (G1), R29.2, U16.11 (DRAIN4)
VOUT_3: CN8.4, Q3.4 (D2)
VOUT_3_GATE: Q3.3 (G2), R30.2, U16.4 (DRAIN1)
VOUT_4: CN8.5, Q3.6 (D1)
VOUT_4_GATE: Q3.1 (G1), R19.2, U16.3 (DRAIN0)

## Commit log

2024-02-12 Added possibility to select CN10 levels via solder jumpers
    [open-control-board.kicad_pcb, open-control-board.kicad_sch]
2024-02-22 Cheaper resistors
    [open-control-board.kicad_pcb, open-control-board.kicad_sch, untitled.kicad_sch]
2024-02-24 Split HV board into separate project
    [open-control-board.kicad_pcb, open-control-board.kicad_sch]
2024-02-24 Updated project symbols and footprints
    [1289.step, BK-885.step, open-control-board.kicad_pcb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]
2024-02-24 Clean up schematic and create PDF
    [open-control-board.kicad_sch]
2024-02-24 Added OSHW logo
    [open-control-board.kicad_pcb]
2024-03-10 Tag R0A
    [BOM-open-control-board.csv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]
2024-03-19 R0B changes (WIP)
    [open-control-board.kicad_pcb, open-control-board.kicad_sch]
2024-03-19 Updated schematic
2024-03-19 Add ibom and updated schematic PDF
2024-03-19 Renamed connectors and added a lot of silk screen
    [open-control-board.kicad_pcb, open-control-board.kicad_sch]
2024-03-20 Updated PCB with screw holes
    [open-control-board.kicad_pcb]
2024-03-20 Changed mounting holes to M2 (to match HV board) and use actual footprints
    [open-control-board.kicad_pcb, open-control-board.kicad_sch]
2024-03-24 Added optional 5V level shifting for CN12-13
    [open-control-board.kicad_pcb, open-control-board.kicad_sch]
2024-03-26 Added test points for unused IO
    [open-control-board.kicad_pcb, open-control-board.kicad_sch]
2024-03-26 Minor updates
    [open-control-board.kicad_pcb]
2024-03-29 Added preliminary gerbers for r0b
    [BOM-open-control-board.csv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]
2024-03-29 Removed C43 and C44 from BOM and CPL (these are optional, and only for when ADC2 A0-A1 or A2-A3 are used in differential mode).
    Fixed issue with ADC1 A1 and A3 not being as flexible as they could be. A3 can now properly be untied from CN6, and A1 can either be untied, tied to CN5, or tied to AVCC.
    [BOM-open-control-board.csv, open-control-board.kicad_pcb, open-control-board.kicad_sch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]
2024-03-29 Moved a few components to get a little more clearance for hand-soldering the ESP32-S3
    [open-control-board.kicad_pcb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]
2024-03-30 Switched JP20 to round footprint.
    Removed a bunch of components that’s not supposed to be in the BOM from the Schematic BOM
    [open-control-board.kicad_pcb, open-control-board.kicad_sch]
2024-03-30 Updated Gerbers and ibom
2024-04-25 WIP on no TXS
    [open-control-board.kicad_pcb, open-control-board.kicad_sch]
2024-05-11 Fairly finalized design
    [open-control-board.kicad_pcb, open-control-board.kicad_sch]
2024-05-12 Moved USB connector
    [open-control-board.kicad_pcb]
2024-05-13 Re-added LED and fixed silk screen
    [open-control-board.kicad_pcb, open-control-board.kicad_sch]
2024-05-13 Updated docs
    [open-control-board.kicad_pcb]
2024-05-13 Updated capacitor footprint
    [open-control-board.kicad_pcb, open-control-board.kicad_sch]
2024-05-16 Added more power connectors to CN9
    [open-control-board.kicad_pcb, open-control-board.kicad_sch]
2024-05-17 Cleaned up schematic
    [open-control-board.kicad_sch]
2024-05-29 Added some additional bypass caps for good measure
    [open-control-board.kicad_pcb, open-control-board.kicad_sch]
2024-05-29 Removed stray reference
    [open-control-board.kicad_pcb]
2024-05-29 Added Variegated Coffee logo and URL
    [open-control-board.kicad_pcb]
2024-06-10 Final updates (as sent to manufacturer)
    [BOM-open-control-board.csv, open-control-board.kicad_pcb, open-control-board.kicad_sch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]
2024-07-03 Errata fixes
    [open-control-board.kicad_pcb, open-control-board.kicad_sch]
